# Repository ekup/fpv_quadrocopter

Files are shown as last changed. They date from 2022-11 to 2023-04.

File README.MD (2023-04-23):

# FPV квадрокоптер-долголет.

Описана моя реализация проекта квадрокоптера-долголета на базе проекта Юлиана RCSchoolmodels.

ВАЖНО! Это не инструкция, а скорее дневник сборки.

Автор изначального проекта: [Юлиан Гиневский RCSchoolmodels](https://vk.com/rcschoolmodelsylian).

Видео, на основе которого сделан проект: [Лучший квадрокоптер-долголет для начинающего! Как собрать, настроить и сделать первый полет!](https://www.youtube.com/watch?v=GBRnG4-c_cc).

Сборка началась 18.11.2022 г. по мере поступления деталей. Описание дополняется...

[Компоненты](components.md)

[STL модели для печати](stl.md)

[Схема подключения компонентов к полетнику](scheme.md)

[Процесс сборки](assembly.md)

[Настройка](settings.md)

Фото в сборке:

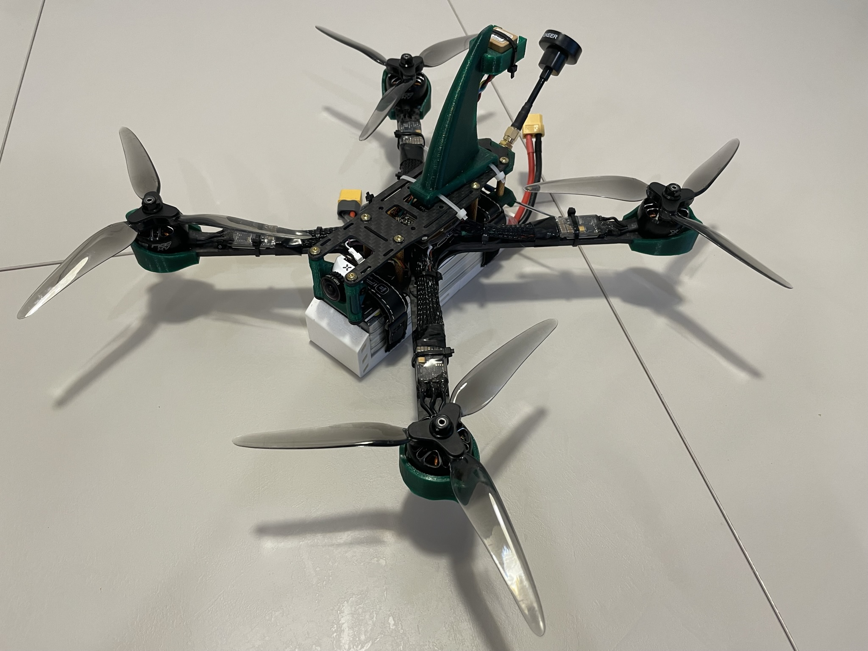
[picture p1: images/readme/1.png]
[](images/readme/1.png)

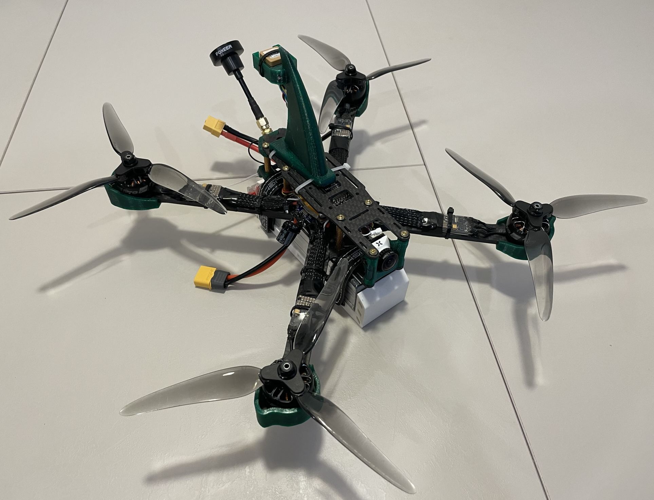
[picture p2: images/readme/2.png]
[](images/readme/2.png)

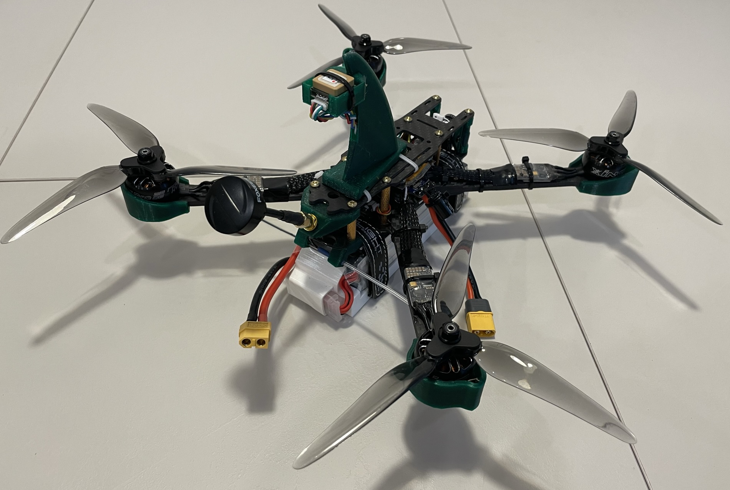
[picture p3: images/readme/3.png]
[](images/readme/3.png)

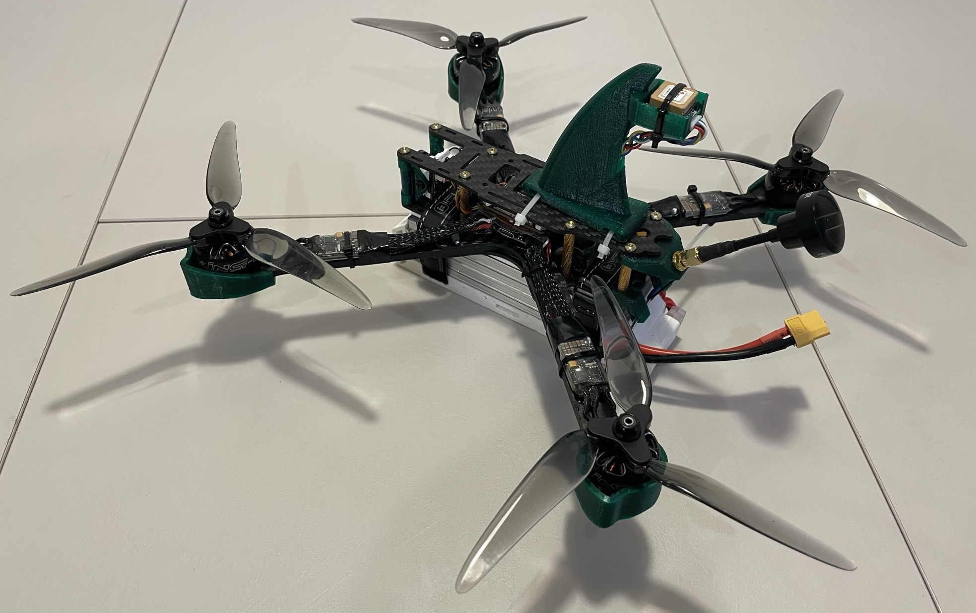
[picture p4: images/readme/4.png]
[](images/readme/4.png)

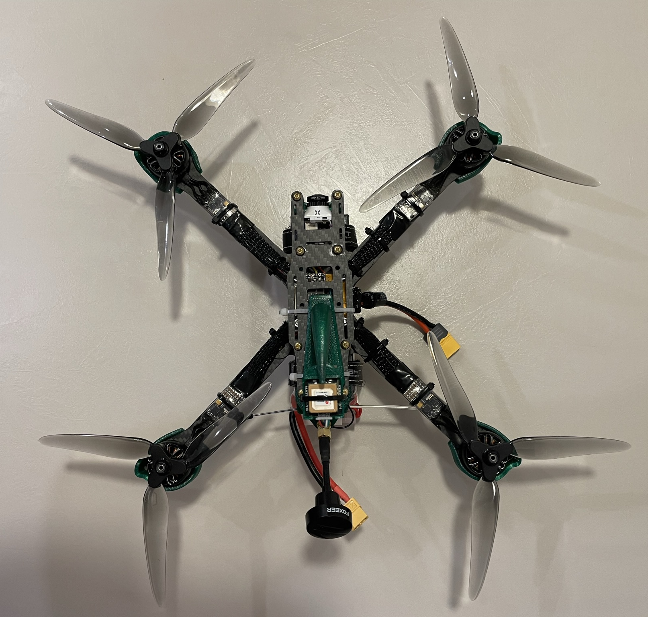
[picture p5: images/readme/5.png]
[](images/readme/5.png)

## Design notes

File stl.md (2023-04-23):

# STL модели для печати

## Крепление антенны видео передатчика

[STL](3d/iflight-sma-mount.stl) - первый вариант

[STL](3d/iflight-sma-mount_new.stl) - доработанный вариант. Уменьшено расстояние от видеопередатчика до антенны чтобы кабель не был внатяг.

Использован проект [Iflight SMA Mount XL5,XL6,XL7,XL8](https://www.thingiverse.com/thing:3726536) от [TrailandScale](https://www.thingiverse.com/trailandscale/designs).

Напечатал из PETG пластика.

## Крепление антенны приемника управления

Разработал сам. 

- [STL](3d/fpv_tbs_mount.stl)

- [DWG](3d/fpv_tbs_mount.dwg)

- [SolidWorks](3d/fpv_tbs_mount.sldprt)

Напечатал из PETG пластика.

## Защита двигателя

- [STL1](3d/left_motor_guard.stl) - 2 шт
- [STL2](3d/right_motor_guard.stl) - 2 шт

Использован проект [XL7 v2 frame motor guard](https://www.thingiverse.com/thing:4860244) от [KingMouse](https://www.thingiverse.com/kingmouse/designs).

Напечатал из PETG пластика.

##  Крепление GPS

[STL](3d/gps_shark.stl)

Использован проект [Holder of Matek GPS M8Q-5883 for drone](https://www.thingiverse.com/thing:5235280) от [iBuilder](https://www.thingiverse.com/ibuilder/designs) (вариант 1).

Напечатал из PETG пластика.

##  Крепление камеры

[STL](3d/soporte_micro_xl7.stl)

Использован проект [iFlight XL5 XL6 XL7 FPV Micro Cam Mount](https://www.thingiverse.com/thing:2844896) от [Atrapao](https://www.thingiverse.com/atrapao/designs).

Напечатал из PETG пластика.

## Защита аккумулятора

Разработал сам.

- [STL](3d/accum_protector.stl)

- [SolidWorks](3d/accum_protector.sldprt)

Напечатал из TPU пластика.

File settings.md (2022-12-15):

# Настройка

## Пульт, приемник

### Обновление прошивки пульта и модуля R9M

Обновлял прошивку пульта и внутренний мультипротокольный модуль по [инструкции](https://oscarliang.com/flash-edgetx/). 
В пульте уже была установлена EdgeTX, обновил до последней версии (2.8.0).

Прошивку для модуля R9M 2019 скачал с [официального сайта](https://www.frsky-rc.com/r9m-2019/) (ACCST FIRMWARE - R9M FLEX) 

### Обновление прошивки приемника R9 mini

Прошивку скачал с [официального сайта](https://www.frsky-rc.com/r9-mini/) (ACCST FIRMWARE - R9Mini FLEX)

Для прошивки с помощью пульта TX16S приемник надо подключить вместо ВЧ модуля как на фото:
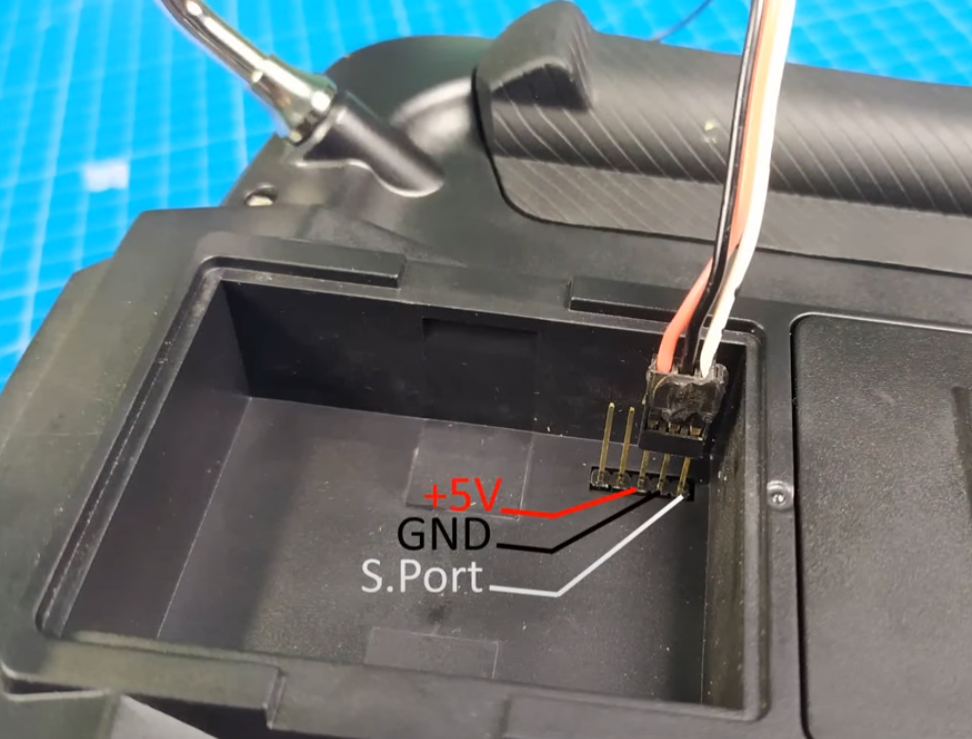
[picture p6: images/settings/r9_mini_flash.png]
[](images/settings/r9_mini_flash.png)

В итоге его можно прошивать как внешний модуль.

Видеоинструкция как обновлять пульт, ВЧ модуль и приемник: [Radiomaster TX16S- Как обновить аппаратуру, мультипротокольный ВЧ модуль и приемники.](https://www.youtube.com/watch?v=XBEd9T3Ygg8)

### Связывание пульта и приемника

Сделал по инструкции из приемника. На пульте запустил процедуру привязки (bind), после этого подал питание на приемник, зажав кнопку на нем. После того как загорелся зеленый светодиод - убрал и снова подал питание на приемник.  

## Полетный контроллер

Настраивал по видео Юлиана.

Перед подключением надо обязательно установить Zadig и установить с помощью него драйвера. При подключении полетника к usb для прошивки зажать кнопку у usb-порта (на полетнике).

Версия платы - MATEKF405TE SD. Последняя версия на момент прошивки - 5.1.0.

Выбрал галочку Full chip erase.

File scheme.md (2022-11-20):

# Схема подключения компонентов к полетнику

Описание полетного контроллера на сайте производителя: [F405-TE](http://www.mateksys.com/?portfolio=f405-te)

## Распиновка от производителя:

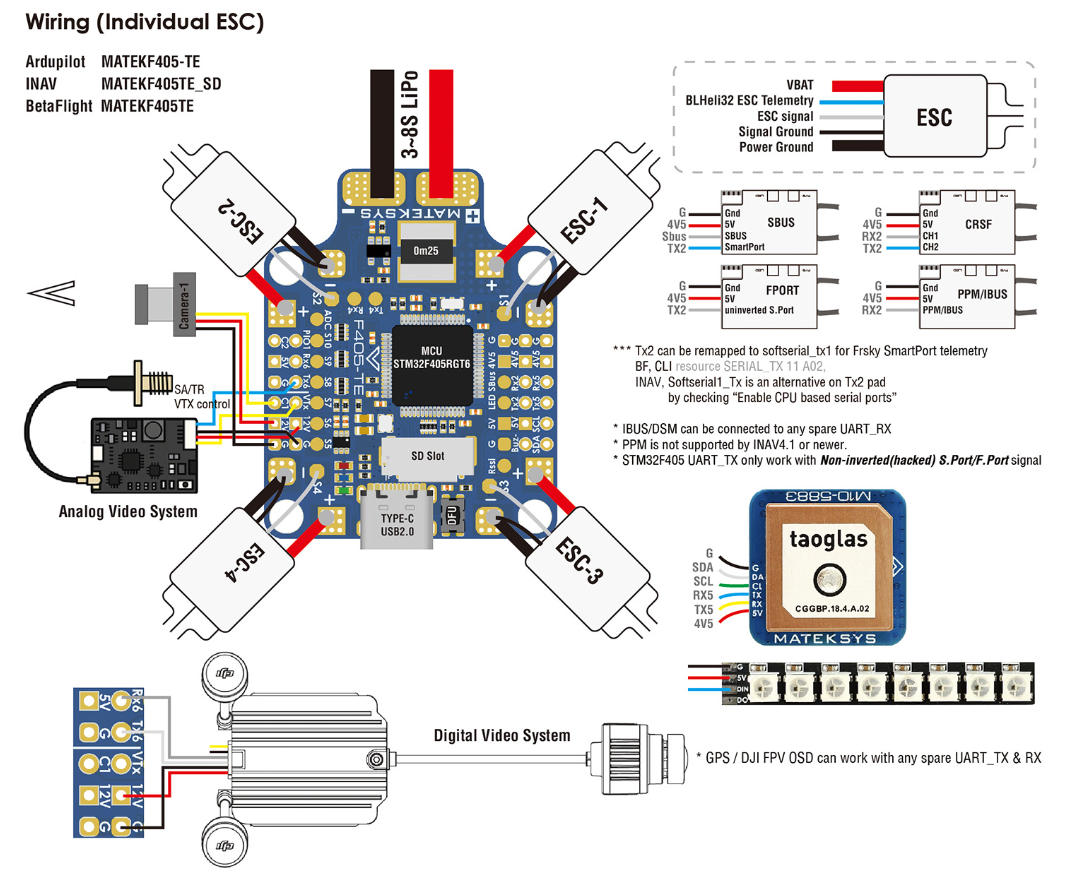
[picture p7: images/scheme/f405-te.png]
[](images/scheme/f405-te.png)

## Камера

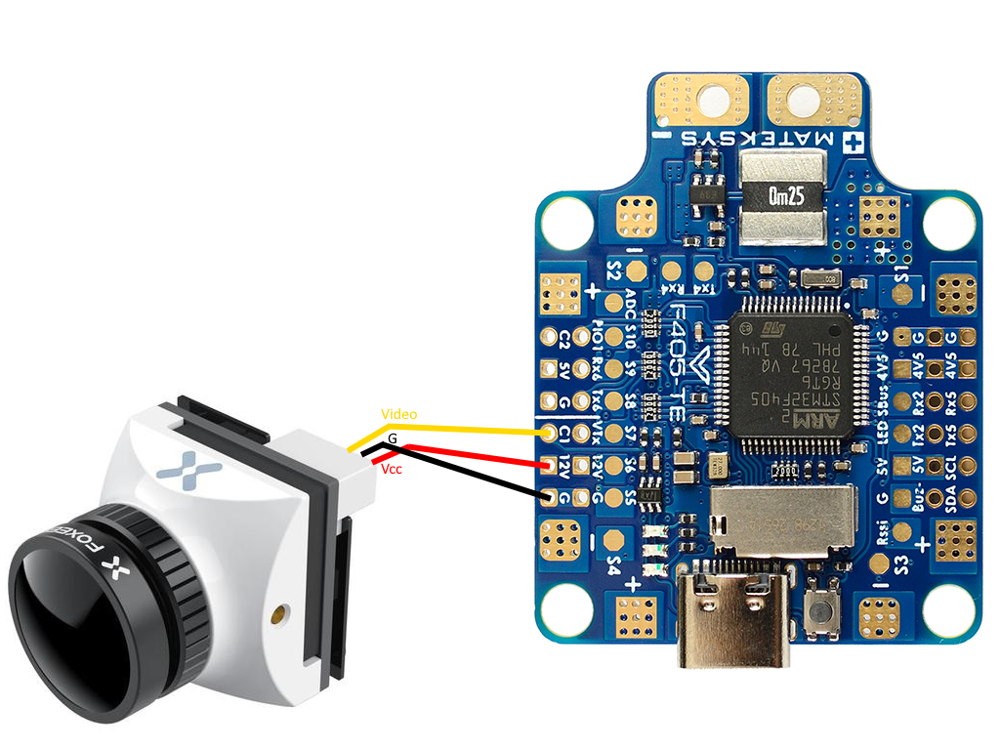
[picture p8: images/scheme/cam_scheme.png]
[](images/scheme/cam_scheme.png)

## Передатчик видео

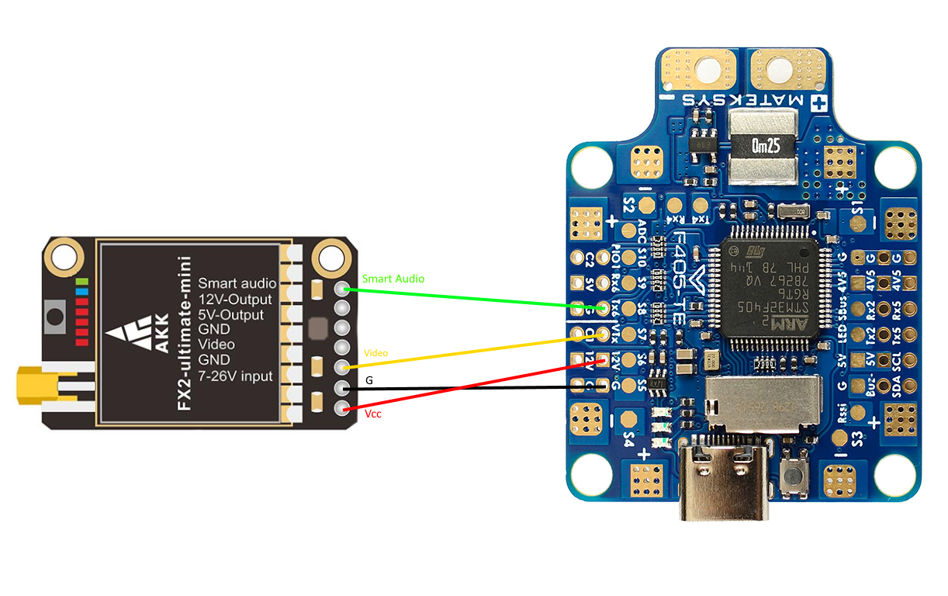
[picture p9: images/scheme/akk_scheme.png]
[](images/scheme/akk_scheme.png)

## Приемник

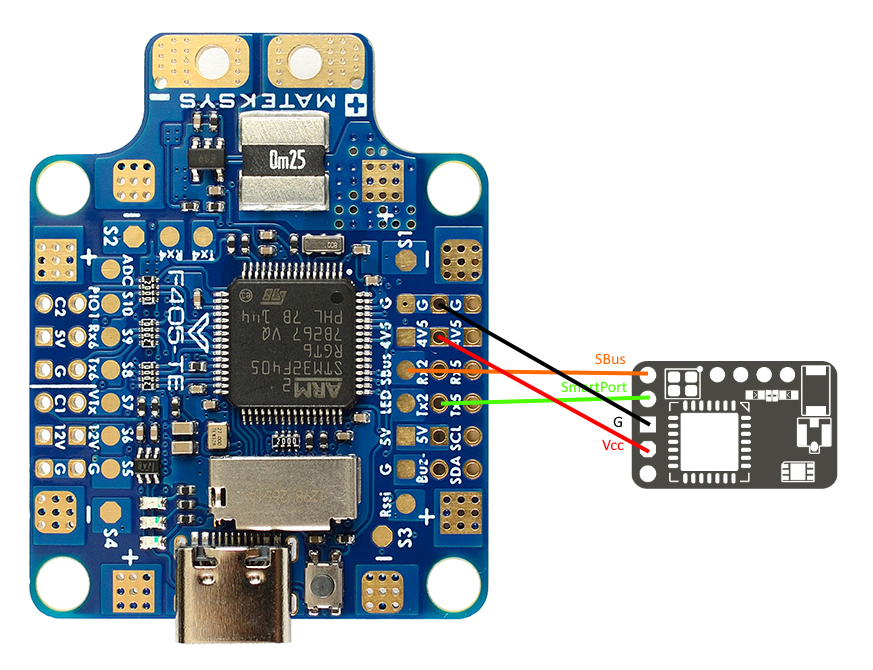
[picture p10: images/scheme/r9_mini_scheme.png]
[](images/scheme/r9_mini_scheme.png)

## Gps

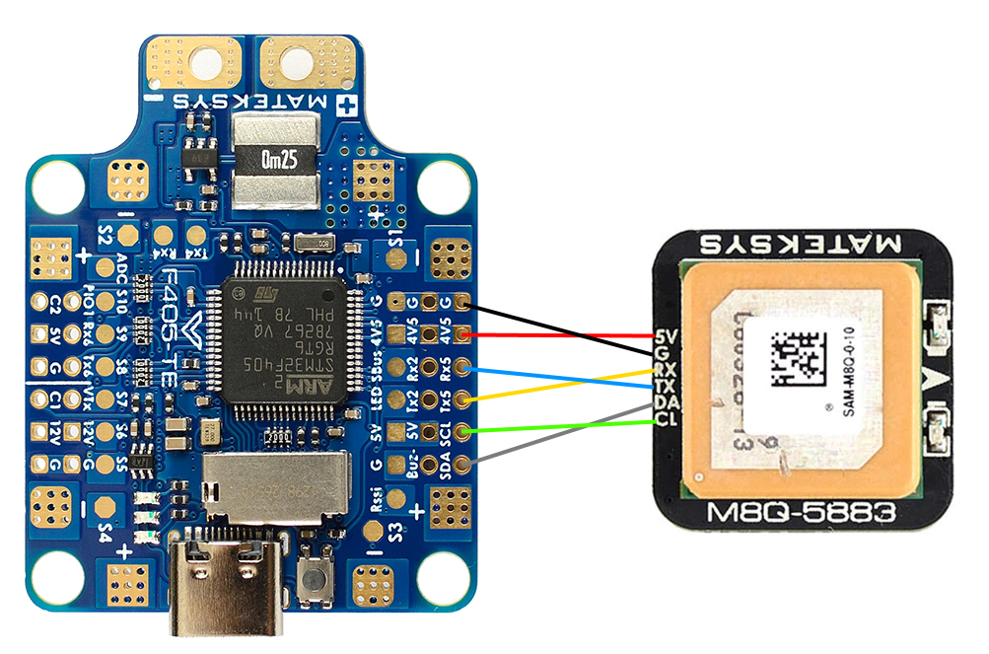
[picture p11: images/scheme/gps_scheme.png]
[](images/scheme/gps_scheme.png)

## Бузер (пищалка)

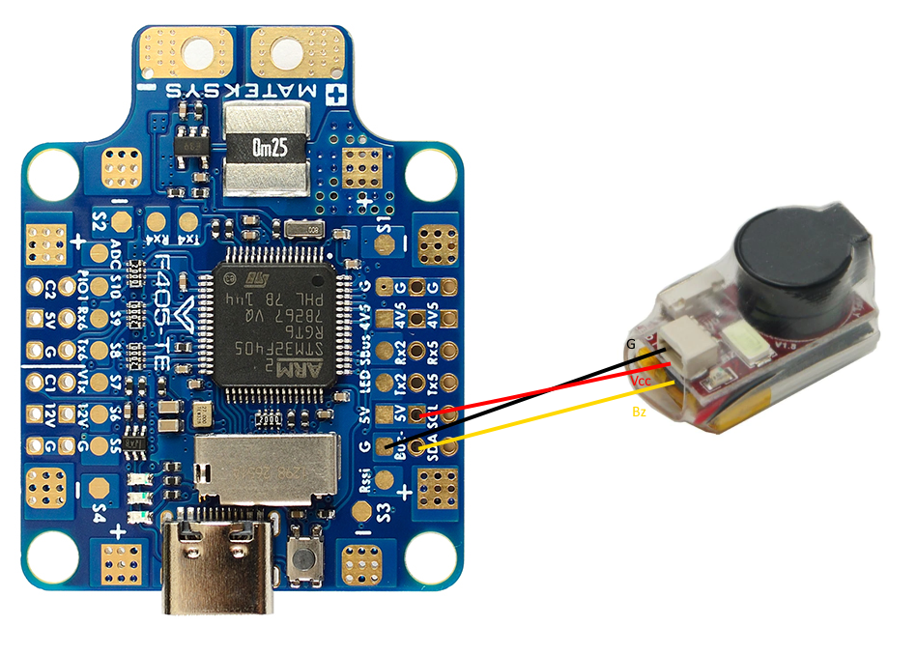
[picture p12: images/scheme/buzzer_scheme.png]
[](images/scheme/buzzer_scheme.png)

## Esc

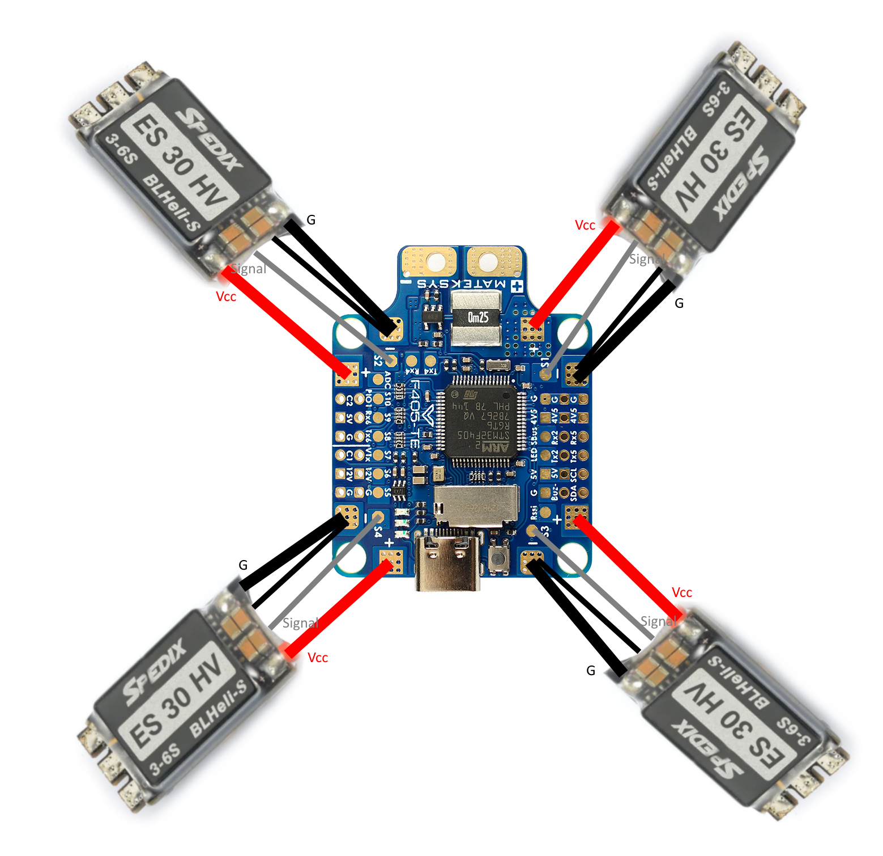
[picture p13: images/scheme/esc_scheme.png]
[](images/scheme/esc_scheme.png)

## Общая схема подключения компонентов

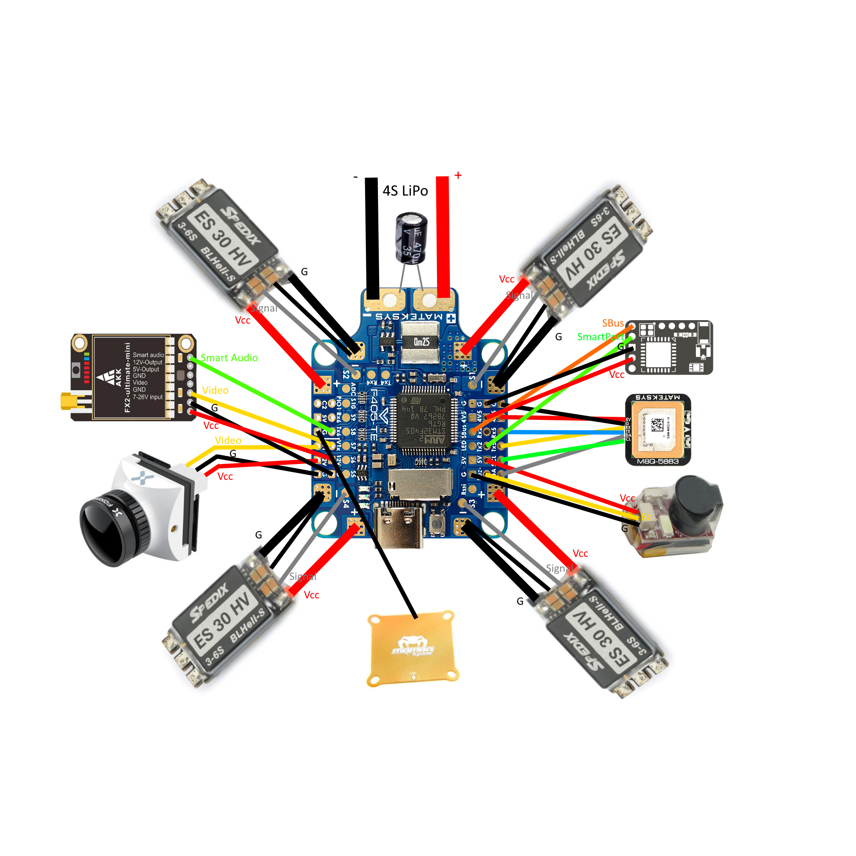
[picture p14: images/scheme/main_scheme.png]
[](images/scheme/main_scheme.png)

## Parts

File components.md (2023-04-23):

# Компоненты

Перечислил все компоненты и материалы, приобретенные для сборки. Указал ссылки, где брал (некоторые могут быть уже недоступными), цены, полное название и фото.

| Что | Название | Ссылка | Цена на момент покупки | Примечание | Фото |
|:---|:---|:---|:---:|:---|:---:|
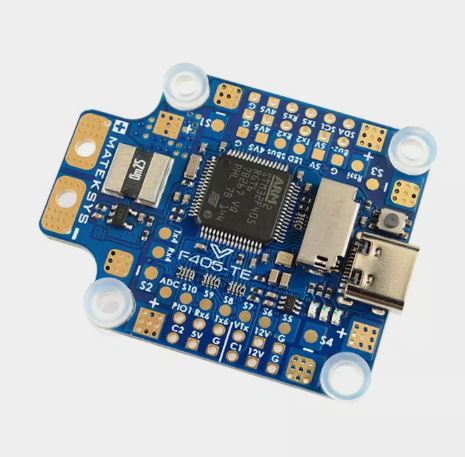
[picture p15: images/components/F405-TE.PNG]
| Полетный контроллер | MATEK F405-TE | [aliexpress](https://aliexpress.ru/item/1005004831870044.html?sku_id=12000030652544326) | 3 930,26 ₽ (17.10.2022) | Официальная замена Matek F405-SE (который больше не производится) | [](images/components/F405-TE.PNG) |
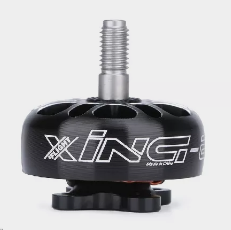
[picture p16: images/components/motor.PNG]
| Моторы | iFlight XING E PRO 1700kv | [aliexpress](https://aliexpress.ru/item/1005004457462713.html?sku_id=12000029801678655) | 3 796,68 ₽ за 4 штуки (17.10.2022) | | [](images/components/motor.PNG) |
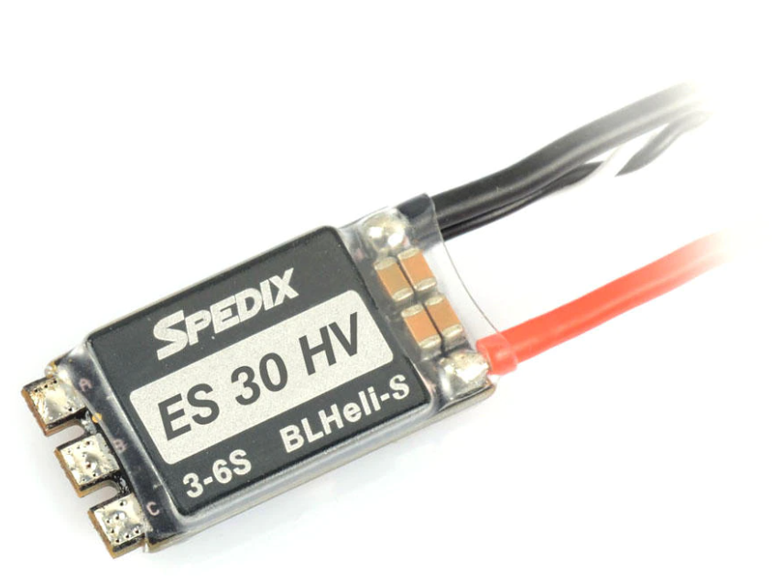
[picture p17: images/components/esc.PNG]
| Регуляторы оборотов | SPEDIX ES30 HV 30A 3-6S blheli | [aliexpress](https://aliexpress.ru/item/4000097311807.html) | 3 653,25 ₽ за 4 штуки (17.10.2022) | | [](images/components/esc.PNG) |
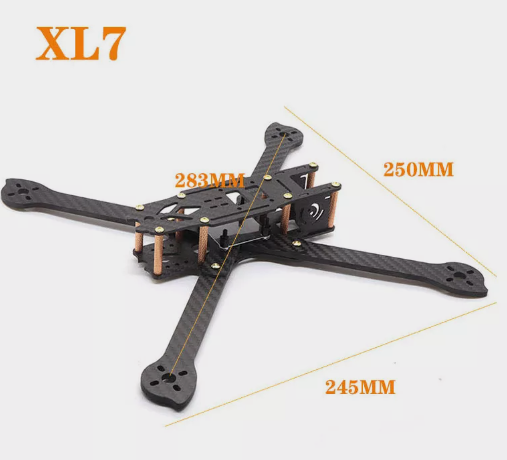
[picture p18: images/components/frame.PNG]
| Рама | HSKRC 3K Углеволокно XL7 294 мм | [aliexpress](https://aliexpress.ru/item/1005001875289273.html?sku_id=12000017986564065) | 1 750,69 ₽ (17.10.2022) | | [](images/components/frame.PNG) |
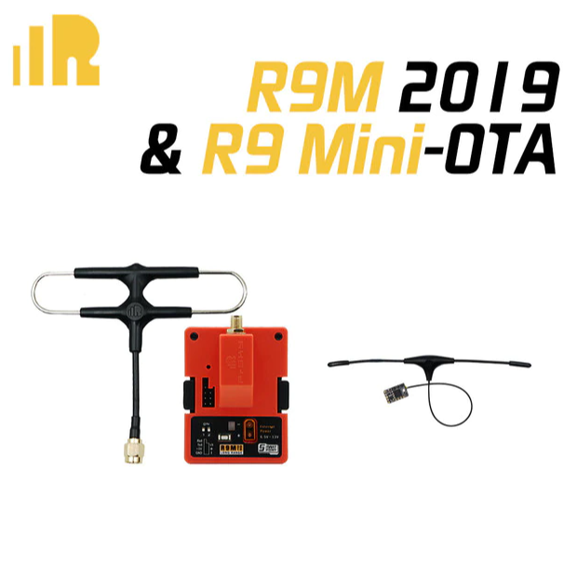
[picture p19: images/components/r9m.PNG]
| Приемник/передатчик управления | R9M R9Mini | [aliexpress](https://aliexpress.ru/item/4001091517804.html?sku_id=10000014316110002) | 4 703,66 ₽ (17.10.2022) | | [](images/components/r9m.PNG) |
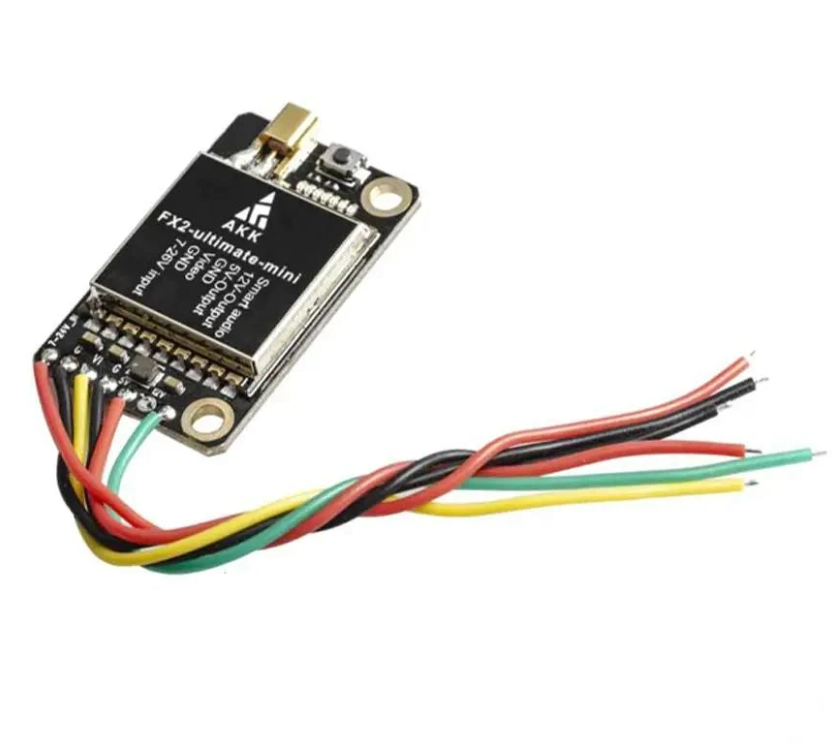
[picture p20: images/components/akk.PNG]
| Передатчик видео | AKK FX2 Ultimate | [aliexpress](https://aliexpress.ru/item/1005003077821412.html?sku_id=12000029792505788) | 1 610,07 ₽ (17.10.2022) | | [](images/components/akk.PNG) |
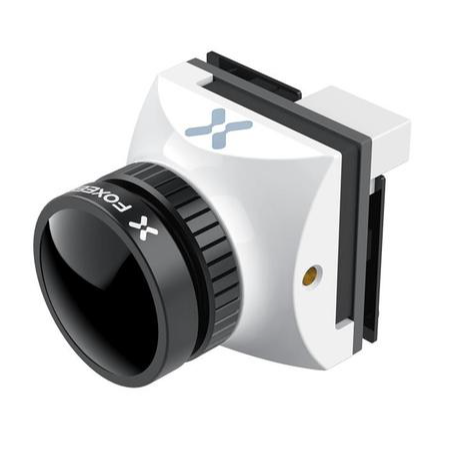
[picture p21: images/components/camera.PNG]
| Полетная камера | Foxeer микро Беззубик | [aliexpress](https://aliexpress.ru/item/1005003150239649.html?sku_id=12000024369664180) | 2 389,80 ₽ (17.10.2022) | | [](images/components/camera.PNG) |
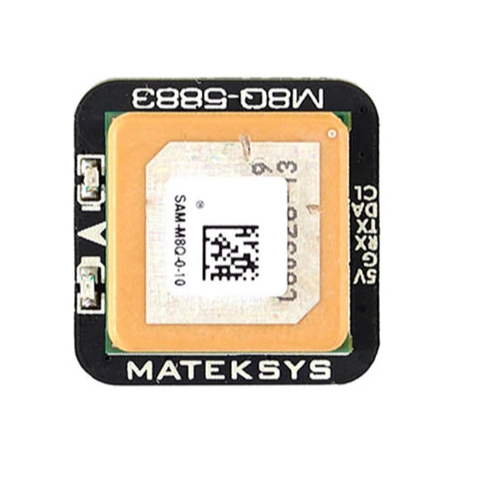
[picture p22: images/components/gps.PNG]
| GPS | Matek QMC5883L | [aliexpress](https://aliexpress.ru/item/32975521759.html?sku_id=12000028028740506) | 2 294,18 ₽ (17.10.2022) | | [](images/components/gps.PNG) |
| Бузер (пищалка) | VIFLY Finder 2 | [aliexpress](https://aliexpress.ru/item/1005003341866970.html?sku_id=12000025309423169) | 878,86 ₽ (17.10.2022) | | [](images/components/bozzer.PNG) |
| Антенна (видео) | Foxeer Pagoda Pro 5,8 ГГц 3dBi Omni SMA | [aliexpress](https://aliexpress.ru/item/1005003115223597.html?sku_id=12000024182638165) | 639,81 ₽ (17.10.2022) | | [](images/components/pagoda.PNG) |
| Пропеллеры | Пропеллеры DALPROP складной F7 7051 7X5.1X3 | [aliexpress](https://aliexpress.ru/item/1005003361369602.html?sku_id=12000025403291602) | 1 885,68 ₽ (17.10.2022) | Цена за 8 пар - 4 комплекта |  [](images/components/propellers.PNG)  |
| Плетеный шнур | Оплетка змеиная кожа для защиты проводов 12..24 мм | [ozon](https://www.ozon.ru/product/opletka-zmeinaya-kozha-dlya-zashchity-provodov-12-24-mm-1-metr-chernaya-570415322/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) | 290 ₽ (18.11.2022) | | [](images/components/braid.PNG) |
| Экран | DIATONE MAMBA Interference Shielding FPC Board | [aliexpress](https://aliexpress.ru/item/1005003922899516.html?sku_id=12000027474911467) | 168,54 ₽ (18.11.2022) | | [](images/components/shield.png) |
| Разъем для подключения аккума  | XT60 | [ozon](https://www.ozon.ru/product/razem-xt60-3-para-465510833/) | 497 ₽ (09.11.2022) | Цена за 3 пары | [](images/components/xt60.PNG) |
| Аккумулятор | ZOP 14.8V 4500mAh 4S 45c Lipo | [banggood](https://www.banggood.com/ru/ZOP-Power-14_8V-4500mAh-4S-45C-Lipo-Battery-XT60-Plug-p-1087251.html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) | 1 927,43 (02.11.2022) | Цена за 1. Взял два. | [](images/components/lipo.PNG) |
| Ремни крепления аккумулятора | IFlight, искусственная микрофибра 15x250mm | [aliexpress](https://aliexpress.ru/item/33039878733.html?sku_id=10000000206840138) | 307,64 (25.01.2023) | Цена за 1. Взял два. | [](images/components/belt.PNG) |
| Предохранитель | TBS предохранитель XT60 и XT30 | [aliexpress](https://aliexpress.ru/item/4000190768487.html?sku_id=10000000712814864) | 994,87 ₽ (17.10.2022) | | [](images/components/fuse.PNG) |
| Пульт | RadioMaster TX16S Mark II V4.0 4 в 1 | [aliexpress](https://aliexpress.ru/item/1005004277455135.html?sku_id=12000029799370815) | 12 291,83 ₽ (09.11.2022) | | [](images/components/radiomaster.PNG) |
| Очки | Eachine & Skyzone Cobra X V2 Diversity Version | [banggood](https://www.banggood.com/ru/Eachine-and-Skyzone-Cobra-S-800x480-or-Cobra-X-V2-1280x720-5_8Ghz-48CH-Diversity-Receiver-FPV-Goggles-With-Head-Tracker-60fps-DVR-Built-i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) | 13 893,13 ₽ (02.11.2022) | | [](images/components/cobra.PNG) |
| Сумма | | | 31 803.56 за квадрокоптер<br/>26 184.96 за пульт + очки<br/>Суммарно 57 988.52 | | |

## Дополнительно использовал

| Что | Название | Примечание | Фото |
|:---|:---|:---|:---:|
| Фиксатор резьбы | Герметик фиксатор разъемный | Брал в леруа | [](images/components/locker.PNG) |
| Электроизоляционный лак | PLASTIK-71 | | [](images/components/lak.PNG) |
| Герметик | TIAN Mu 704 черный | Брал в [taggsm](https://taggsm.ru) | [](images/components/704.PNG) |

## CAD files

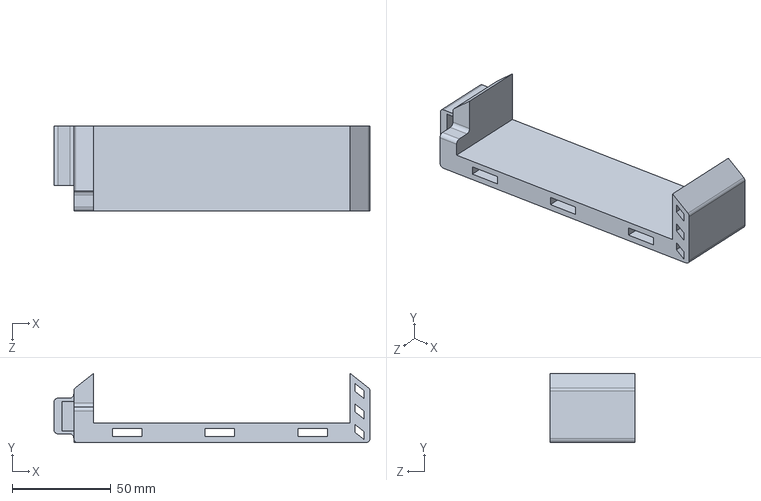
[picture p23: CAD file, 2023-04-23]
3d/accum_protector.sldprt
160.0 x 35.0 x 43.0 mm

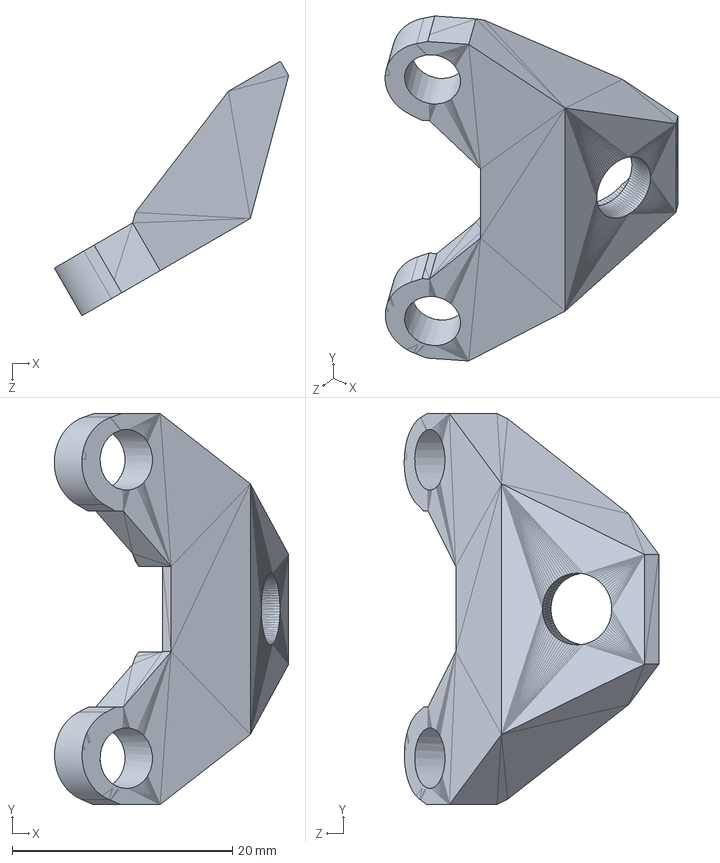
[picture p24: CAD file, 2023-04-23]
3d/iflight-sma-mount_new.SLDPRT
21.3 x 35.5 x 23.1 mm

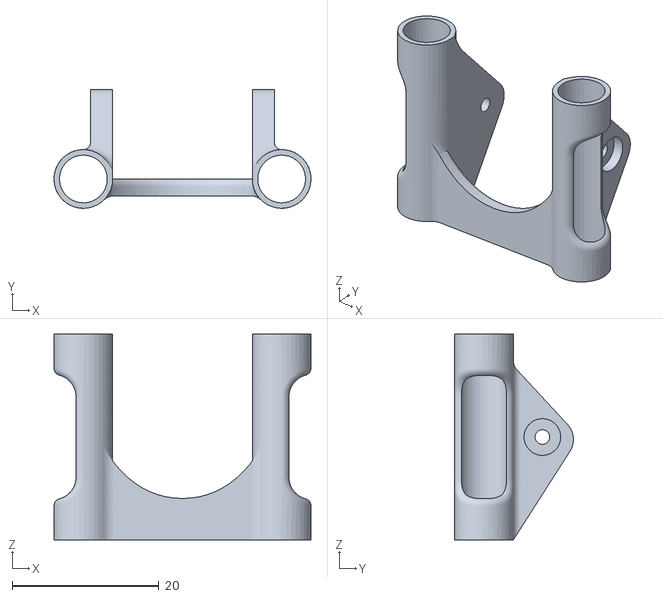
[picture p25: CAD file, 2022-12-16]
3d/soporte_micro_xl7.stl
35.0 x 16.2 x 28.0

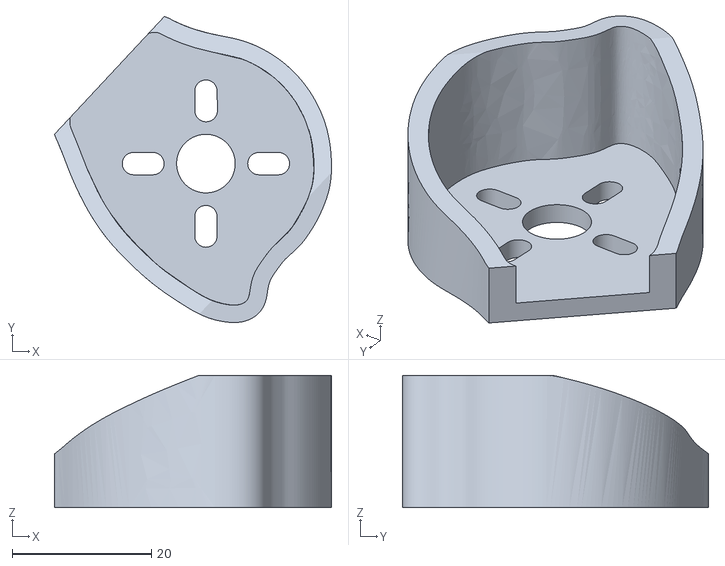
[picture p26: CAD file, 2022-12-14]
3d/right_motor_guard.stl
39.7 x 43.9 x 19.0

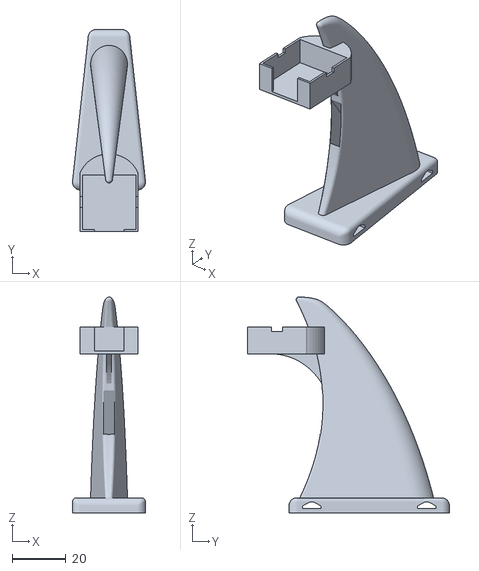
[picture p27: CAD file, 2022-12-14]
3d/gps_shark.stl
27.3 x 75.5 x 80.7

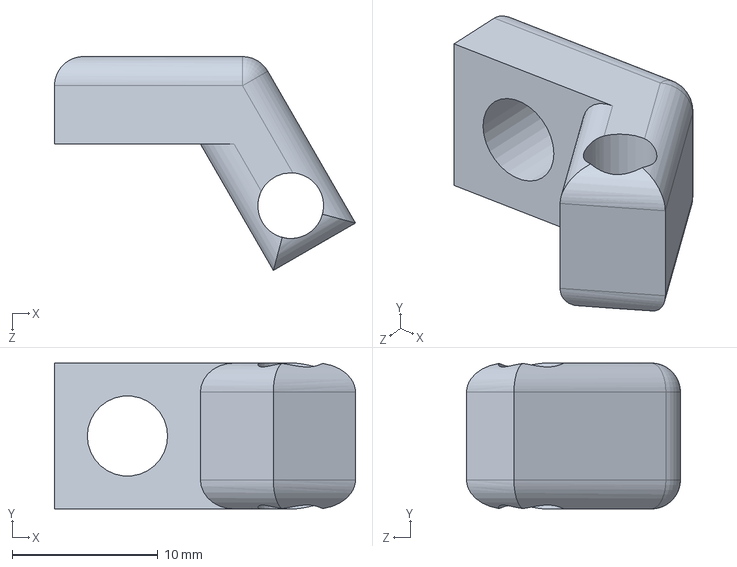
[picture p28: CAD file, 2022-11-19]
3d/fpv_tbs_mount.sldprt
20.6 x 10.0 x 14.7 mm

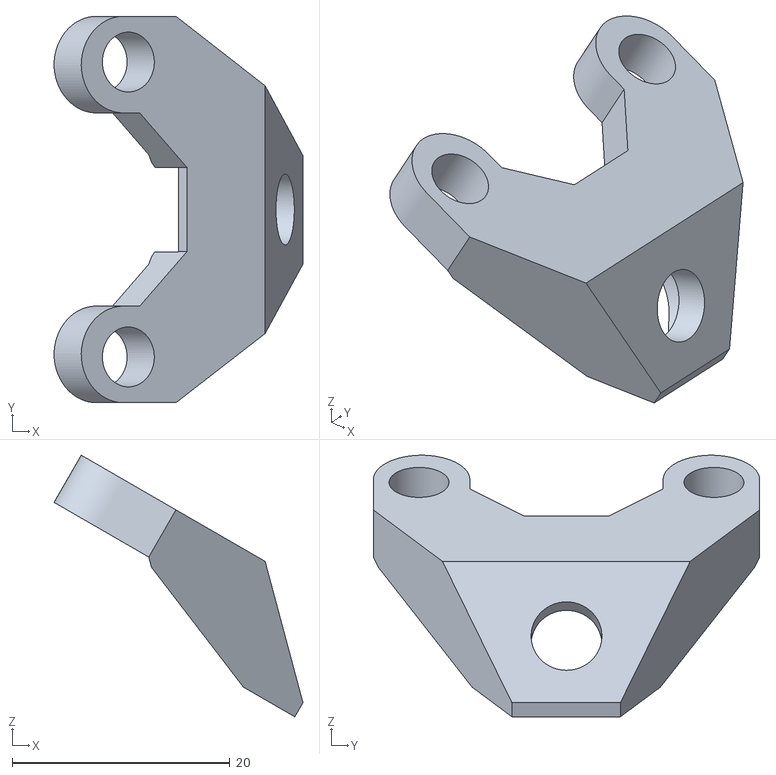
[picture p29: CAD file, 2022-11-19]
3d/iflight-sma-mount.stl
22.9 x 35.5 x 24.0

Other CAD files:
3d/left_motor_guard.stl
3d/accum_protector.stl
3d/fpv_tbs_mount.dwg
3d/fpv_tbs_mount.stl
3d/iflight-sma-mount_new.stl

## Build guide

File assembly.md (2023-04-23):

# Процесс сборки

Для всех винтовых соединений использовал фиксатор резьбы.

1. Собрал нижнюю часть рамы с лучами. Винты для крепления полетника заменил на M3x30.
 
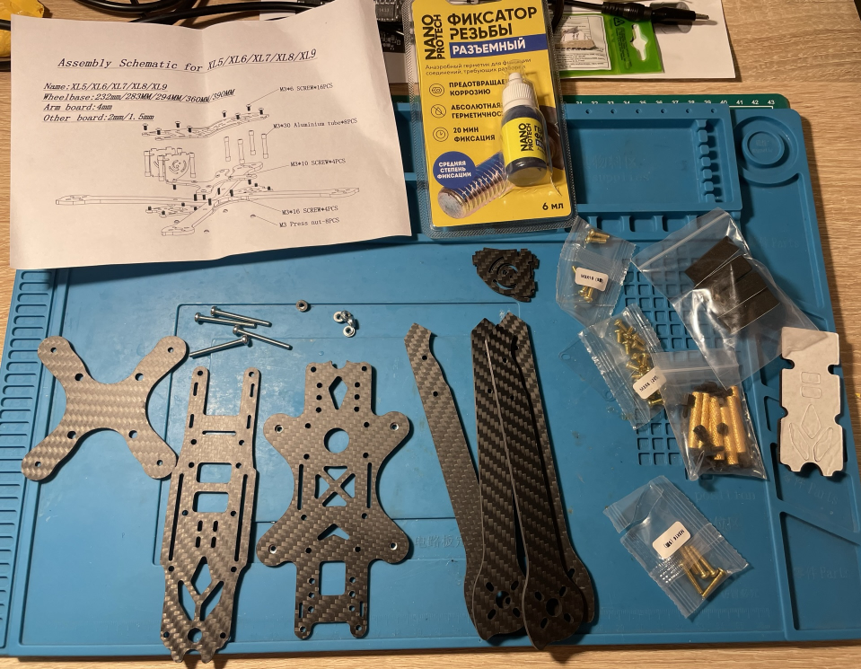
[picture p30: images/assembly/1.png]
[](images/assembly/1.png)

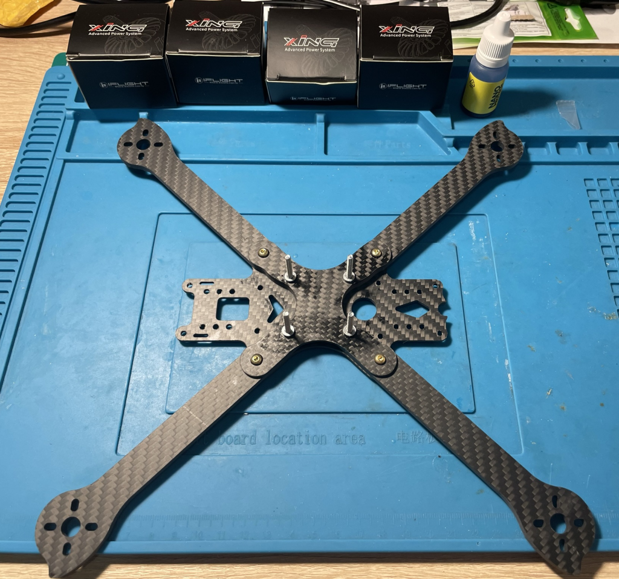
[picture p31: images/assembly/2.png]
[](images/assembly/2.png)

2. Установил моторы.

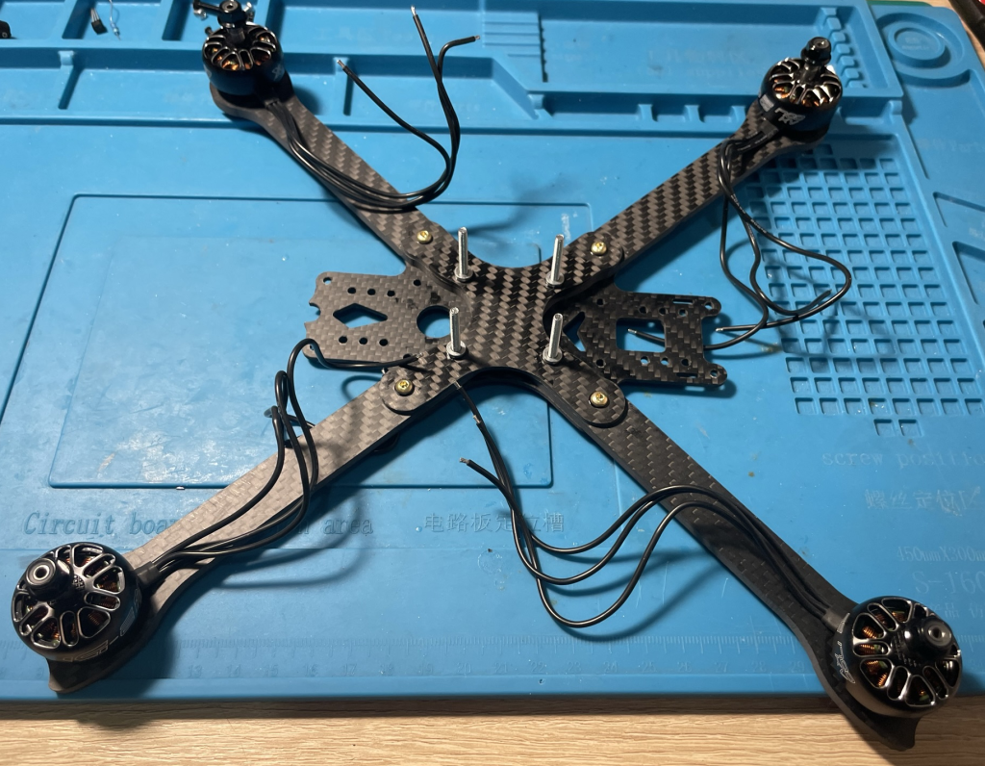
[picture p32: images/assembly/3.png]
[](images/assembly/3.png)

3. Припаял моторы к драйверам.

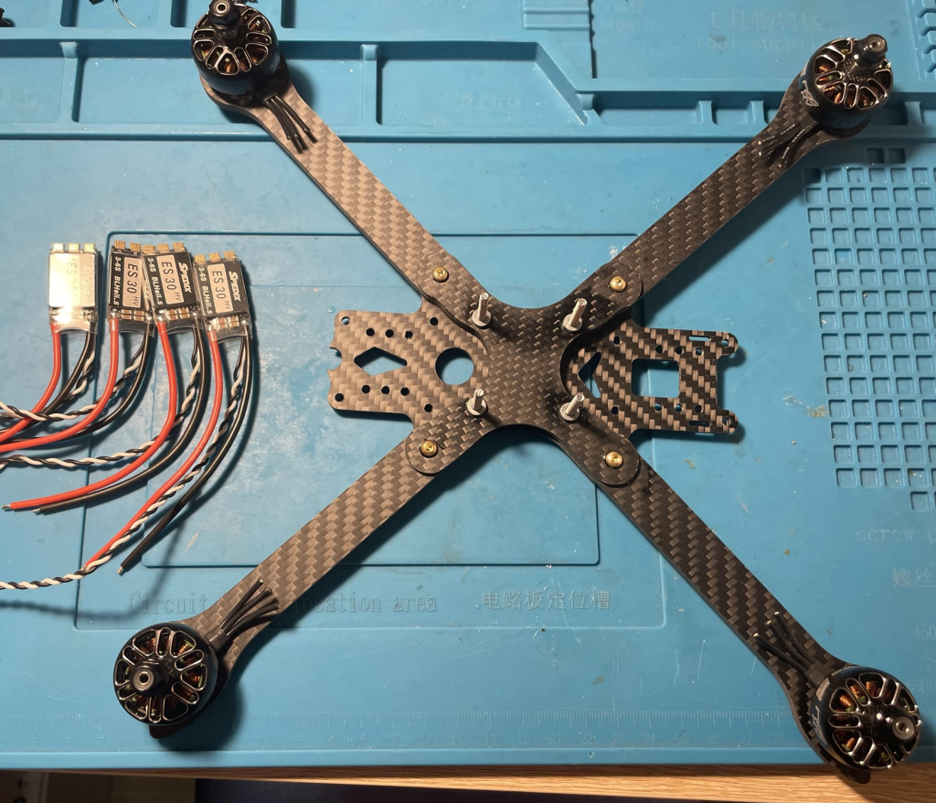
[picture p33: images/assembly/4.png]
[](images/assembly/4.png)

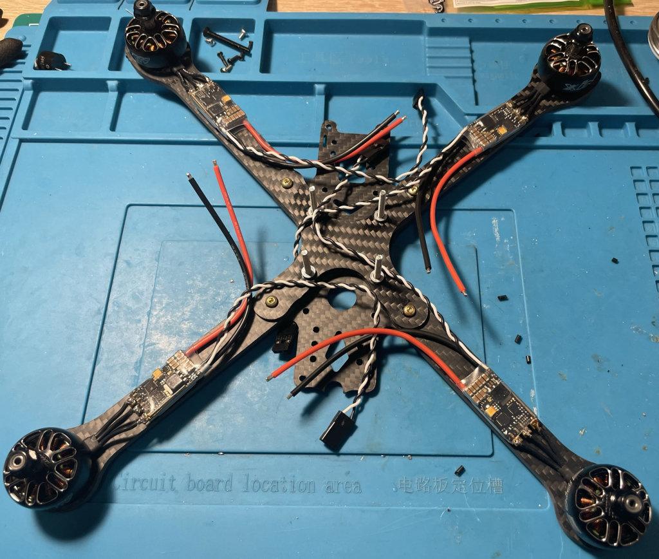
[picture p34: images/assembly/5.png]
[](images/assembly/5.png)

4. Решил поставить защиту моторов. Пришлось их откручивать. Длины комплектных винтов не хватило - заменил их на M3x10 и добавил шайбы, чтобы не продавливался пластик защиты.
 
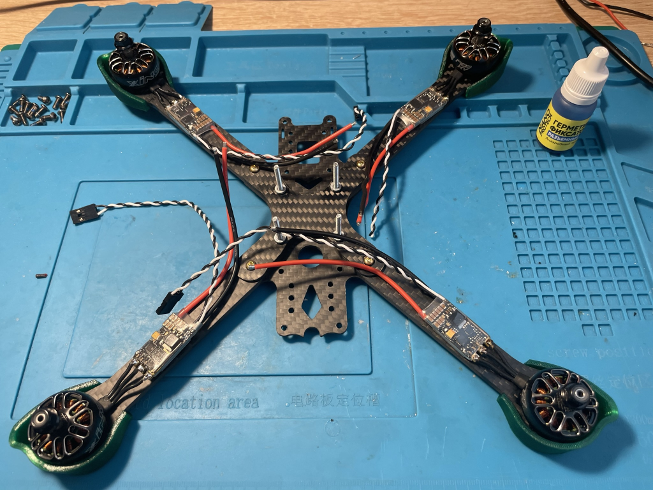
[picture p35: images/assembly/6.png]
[](images/assembly/6.png)

5. Припаял к полетному контроллеру передатчик видео, разъем для камеры и провод для экрана. 

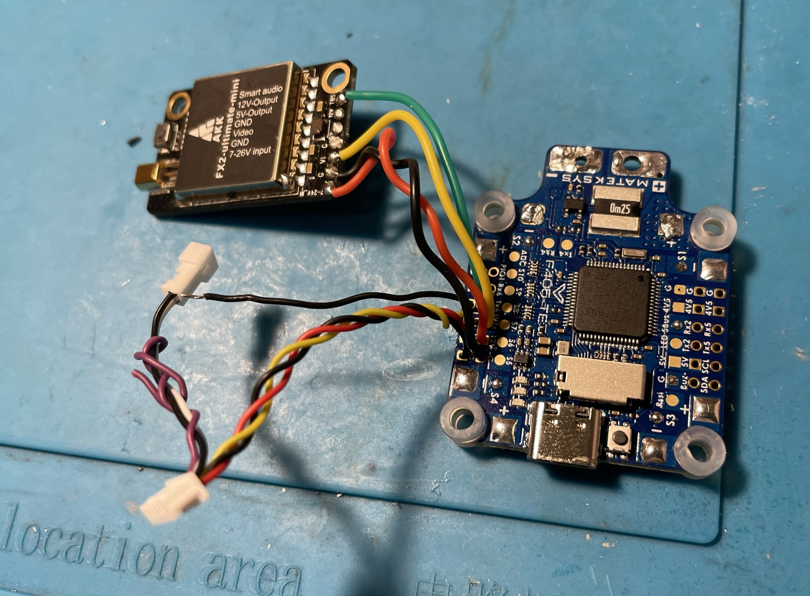
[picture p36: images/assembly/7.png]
[](images/assembly/7.png)

6. Припаял к полетному контроллеру бузер, gps и приемник. Покрыл лаком нижнюю сторону (кроме барометра)

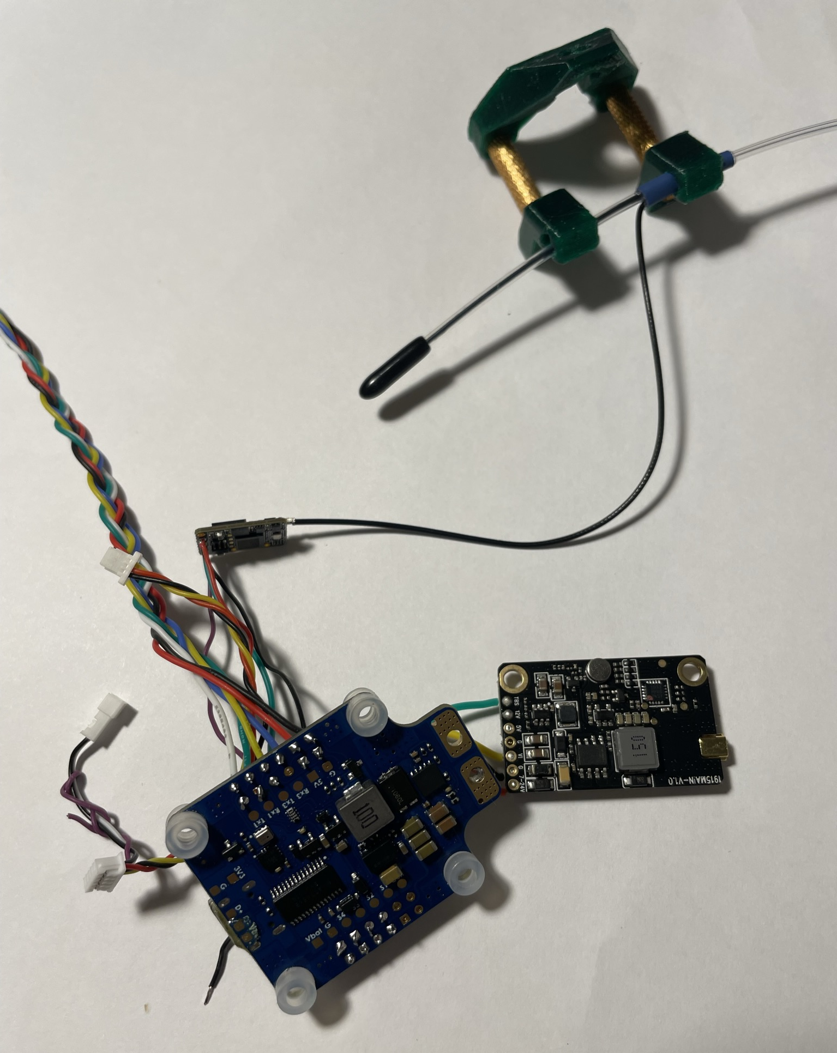
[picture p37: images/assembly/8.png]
[](images/assembly/8.png)

7. Поставил полетник на свое место, припаял регуляторы оборотов. Посадил регуляторы на двухсторонний скотч и стяжки.

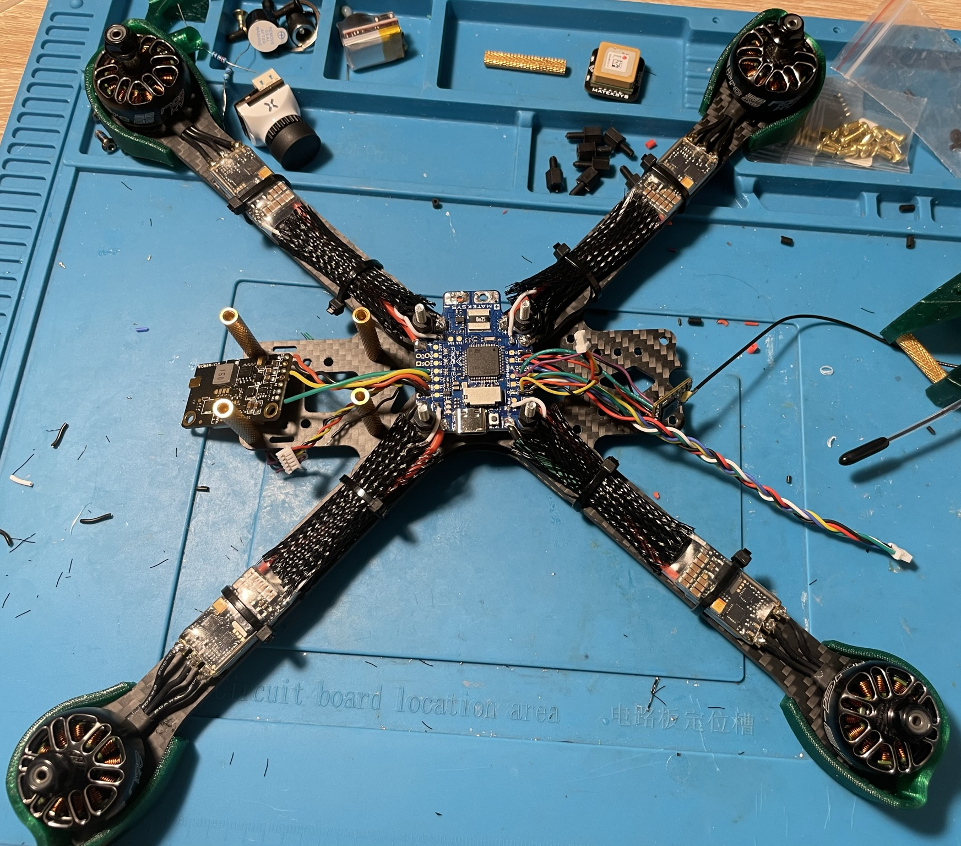
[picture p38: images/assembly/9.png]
[](images/assembly/9.png)

8. Поставил на место крепления для антенн и видеокамеру. Припаял кабель питания и конденсатор на него. Залил контакты герметиком TIAN Mu 704.

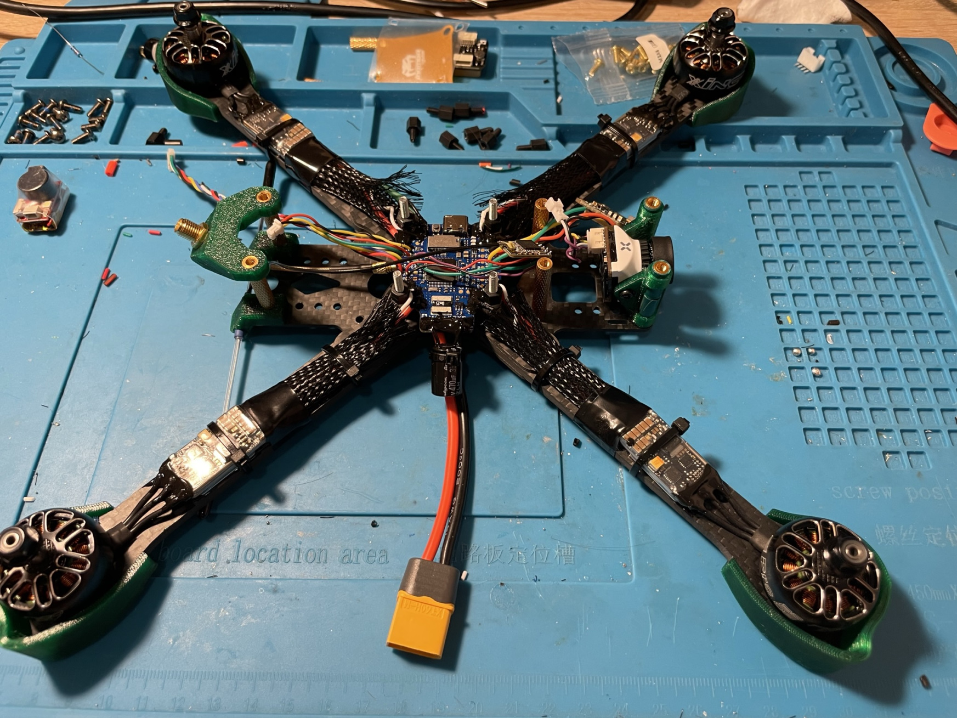
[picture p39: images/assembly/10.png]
[](images/assembly/10.png)

9. Фото дальнейших действий утеряны.  
Между полетным контроллером и видеопередатчиком поставил экранирующую пластинку, подпаял к ней минус с питания. 
Между ней и видеопередатчиком наклеил двухсторонний скотч. Приемник управления приклеил к этому скотчу рядом с видеопередатчиком.
Установил верхнюю часть рамы (винты лучше привинчивать без фиксатора резьбы. Их много и они и так хорошо держатся, а выкручивать их придется регулярно), 
прикрепил к ней плавник на двухсторонний скотч и стяжки. 

[](images/assembly/11.png)

[](images/assembly/12.png)

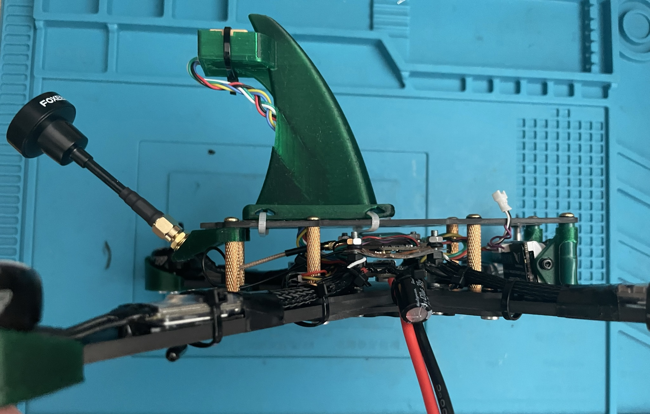
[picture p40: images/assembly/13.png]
[](images/assembly/13.png)

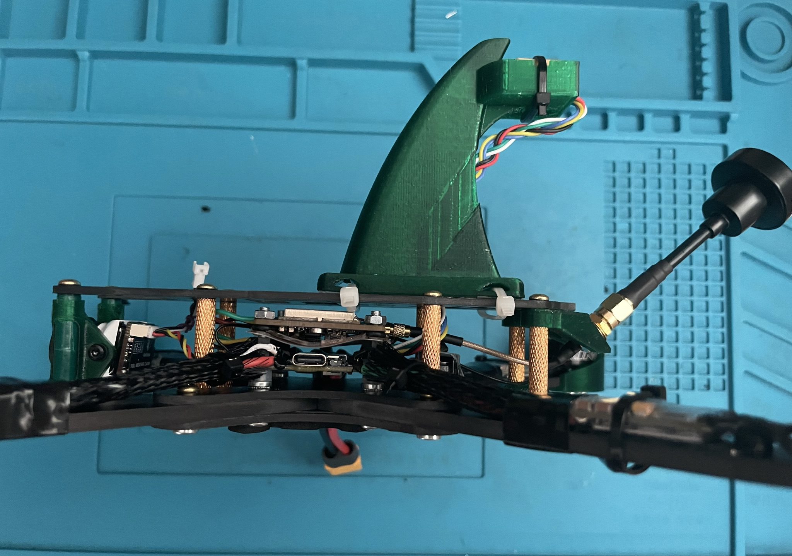
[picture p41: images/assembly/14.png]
[](images/assembly/14.png)

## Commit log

2022-11-19 Assembly, stl
    [fpv_tbs_mount.dwg, fpv_tbs_mount.sldprt, fpv_tbs_mount.stl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]
2022-11-20 esc scheme
2022-12-14 some stls
    [gps_shark.stl, left_motor_guard.stl, right_motor_guard.stl]
2022-12-15 motor guards assembly. Settings.
2022-12-16 cam holder stl. Next assembly steps
    [soporte_micro_xl7.stl]
2022-12-18 Next assembly step
2023-04-23 SMA mount update. Next assembly step
    [iflight-sma-mount_new.SLDPRT, iflight-sma-mount_new.stl]
2023-04-23 Accum protector
    [accum_protector.sldprt, accum_protector.stl]
